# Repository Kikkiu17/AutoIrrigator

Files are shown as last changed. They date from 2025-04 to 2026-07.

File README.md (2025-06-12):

# Il progetto
Alla base del progetto c'è un microcontrollore **STM32G030F6P6**, compatto e dal costo di qualche decina di centesimi, che si interfaccia con un modulo **ESP-01S** per la connessione a Internet. Il microcontrollore può pilotare quattro elettrovalvole assieme a quattro sensori di flusso dell'acqua, uno per ogni tubo. I sensori di flusso permettono di rilevare la presenza di problemi lungo le linee e le quattro valvole consentono di irrigare fino a quattro aree alla volta.

Il tutto è **controllabile da remoto tramite un'app Android**, con la quale si possono aprire o chiudere le valvole manualmente ma si può anche impostare una programmazione per l'apertura e chiusura automatica in base all'orario o al tempo atmosferico. Infatti, il microcontrollore effettua ogni 15 minuti una richiesta all'API Open-Meteo per **ottenere le previsioni meteo della giornata**: se è prevista pioggia, è inutile irrigare, quindi le valvole resteranno chiuse.
# Costruzione
## Hardware
### Circuito stampato
Ho iniziato con l'hardware. Ho sviluppato un circuito elettronico in KiCad in modo che l'STM potesse controllare le valvole e i sensori. Le valvole sono a 12 V e consumano ~600 mA di corrente, quindi ho usato MOSFET AO3400A per poterle controllare con l'STM (i cui pin hanno un output massimo di ~15 mA a 3,3 V). Pure i sensori di flusso operano a 12 V, quindi ho usato gli stessi MOSFET per poterli interfacciare col microcontrollore.

Ho poi stampato in 3D uno stencil per poter spalmare la pasta saldante sui vari pad dei componenti a montaggio superficiale (SMD). Questo perché ordinarlo assieme alle PCB sarebbe costato quasi 20 € in più, mentre così è gratis e il risultato è comunque accettabile. Quindi perché no?

Schema:

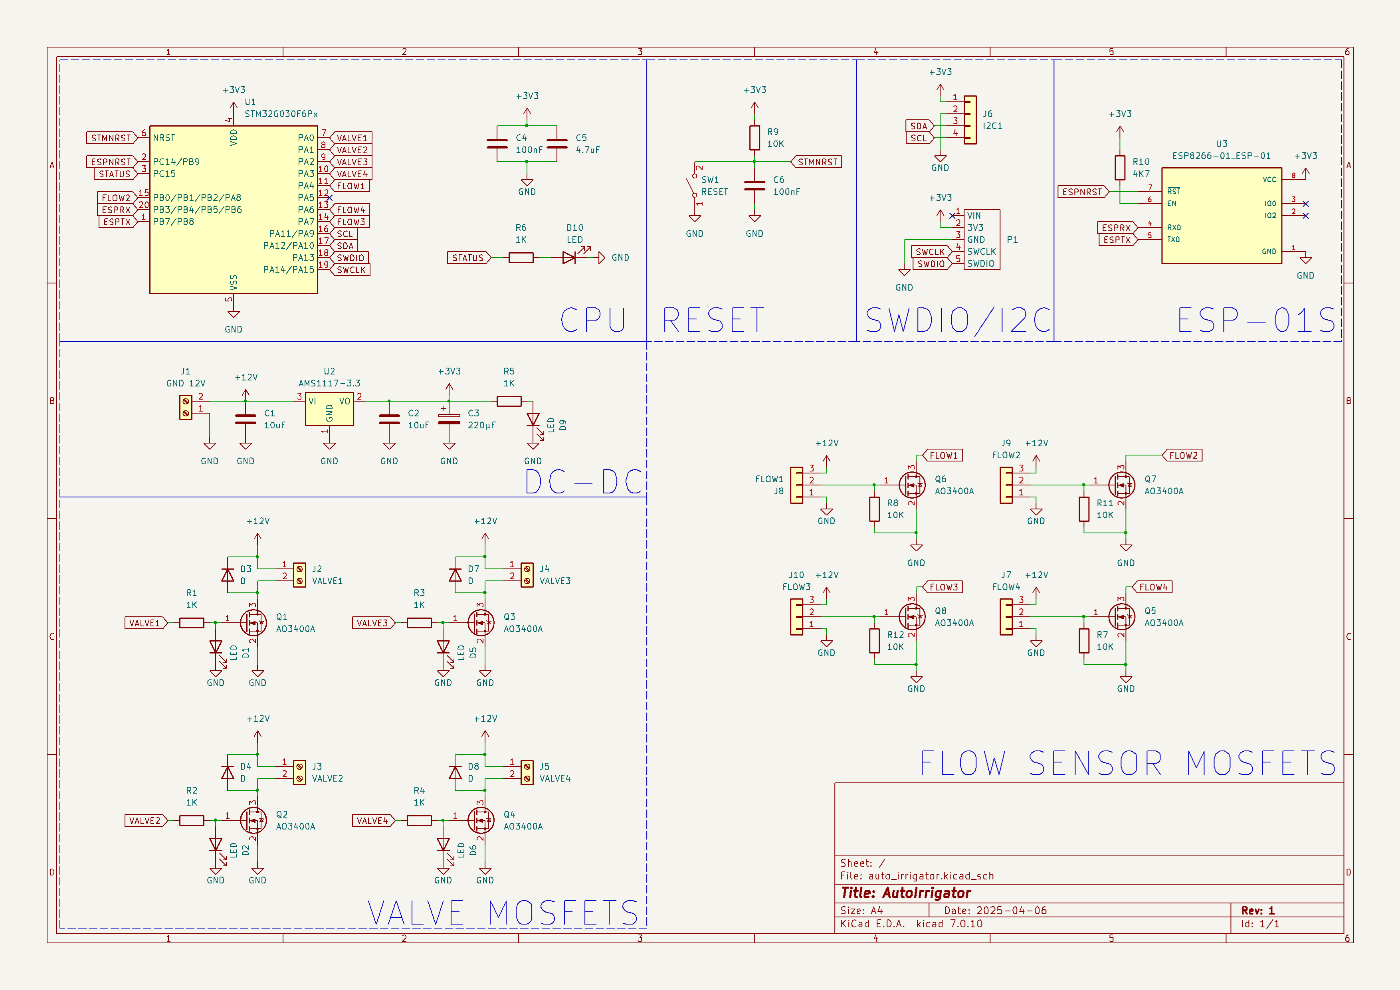
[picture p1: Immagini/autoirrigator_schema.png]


PCB:

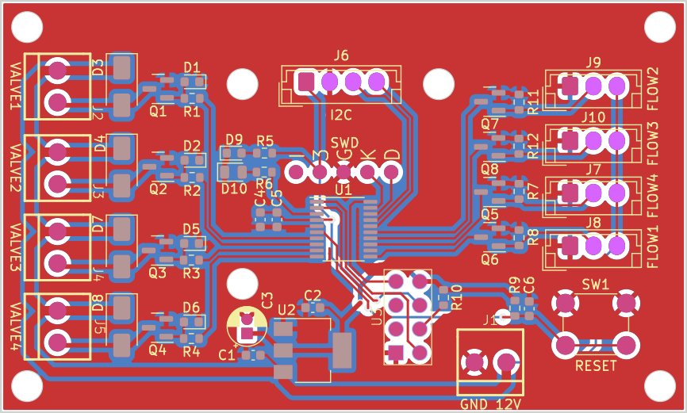
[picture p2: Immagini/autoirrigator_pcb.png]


Stencil fatto in casa


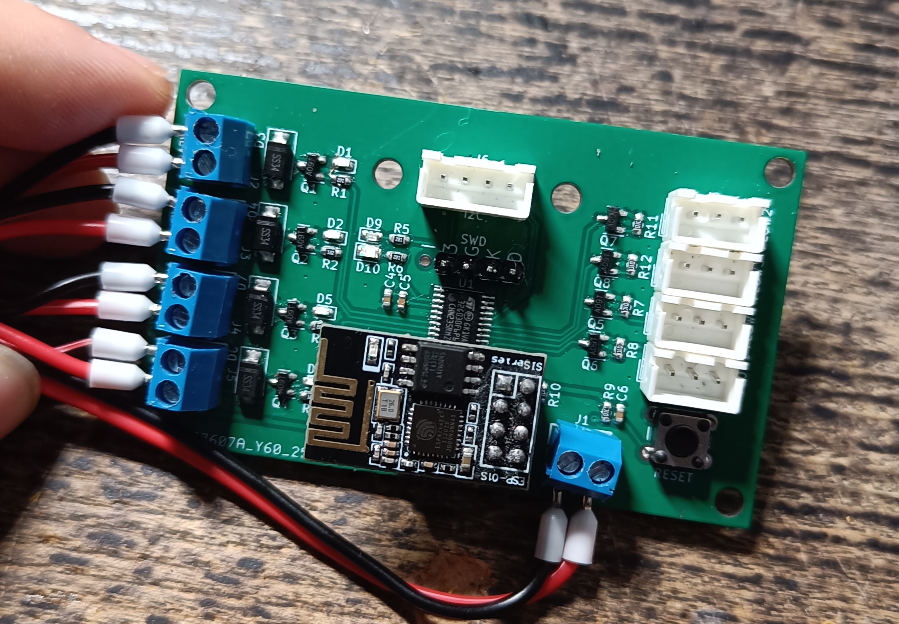
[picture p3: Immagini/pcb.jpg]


### Modello 3D
Mentre aspettavo l'arrivo delle PCB, ho iniziato a creare il modello 3D del progetto, con dei raccordi per le valvole e i sensori. Ho creato un design abbastanza compatto ma comunque semplice da assemblare, con il circuito stampato al centro in modo da poterci collegare tutti i fili comodamente.

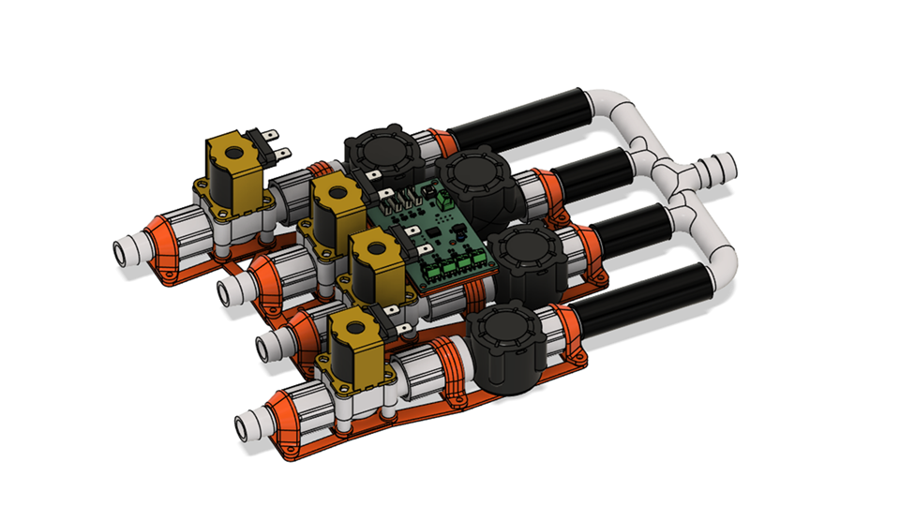
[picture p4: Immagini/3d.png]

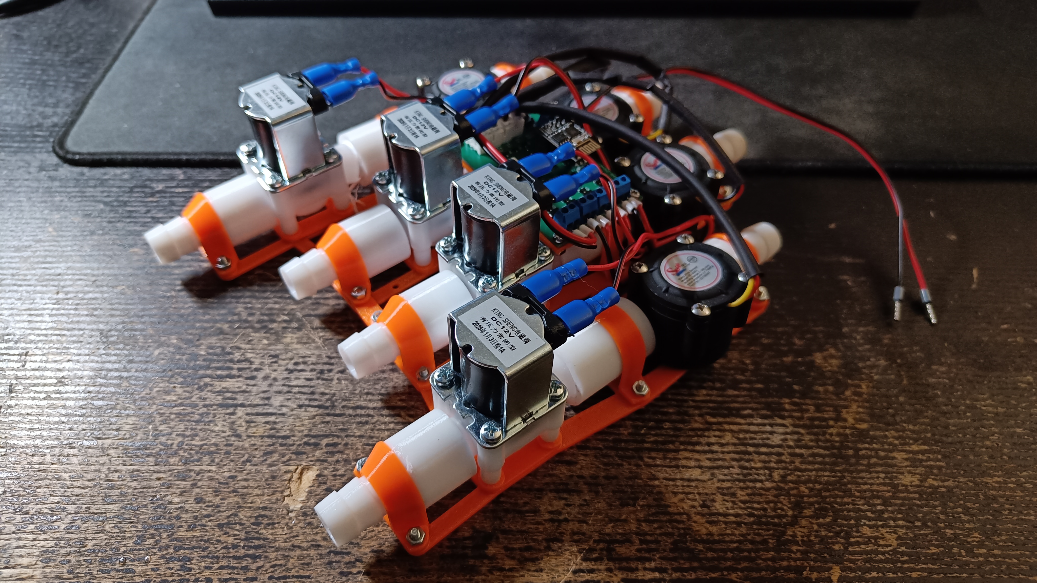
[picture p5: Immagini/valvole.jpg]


## Software
### Firmware embedded
Dopo aver fatto i raccordi e i supporti, sono passato al software. Ho iniziato a scrivere il [mio driver](https://github.com/Kikkiu17/ESP-AT-STM32) per l'ESP-01S dato che non ne ho trovato nessuno online abbastanza semplice da usare compatibile con l'STM32. Il driver sfrutta il DMA dell'STM32 per poter ricevere i dati dell'ESP dalla porta seriale senza usare la CPU, aumentando quindi le prestazioni (in questo caso le prestazioni non sono critiche, ma fa comunque comodo). L'ESP viene connesso alla rete WiFi; viene impostato l'hostname `ESPDEVICE002` per poter essere riconosciuto nella rete; viene impostato il nome `Hub irrigazione`; viene connesso al server NTP in modo da poter ottenere la data e l'ora e infine l'ESP viene impostato in modalità `server` in modo da accettare connessioni remote sulla porta `23`. Poi, nel ciclo while principale, il firmware attende nuove richieste tramite la funzione `WIFI_ReceiveRequest` che dopo verranno gestite.

Grazie ai numerosi timer dell'STM32G030F6P6, ho dedicato tre timer ai quattro sensori di flusso (chiamati FLOW): TIM14 per FLOW1, TIM1 per FLOW2, TIM3 per FLOW3 e FLOW4. In questo modo ho potuto usare quattro pin fisici per ciascun sensore, invece che fare multiplexing coi quattro sensori, rendendo quindi tutto molto più semplice. Imposto i canali timer dei sensori in modalità `Input compare` e abilito gli interrupt per i timer, in modo da ottenere il periodo del segnale PWM dei sensori. Facendo `1/T`, dove T è il periodo, si ottiene la frequenza e dividendola per 7,5 si ottiene il flusso d'acqua in `litri/min`.

Infine ho scritto del codice per connettermi all'API di Open-meteo per ottenere le [previsioni per il giorno corrente](http://api.open-meteo.com/v1/forecast?latitude=45.5582&longitude=9.2149&hourly=precipitation,precipitation_probability&current=precipitation&timezone=auto&forecast_days=1) tramite la funzione `WEATHER_GetForecast`. Le previsioni vengono immagazzinate in degli array in modo da poter accedere facilmente ad esse.

### App Android
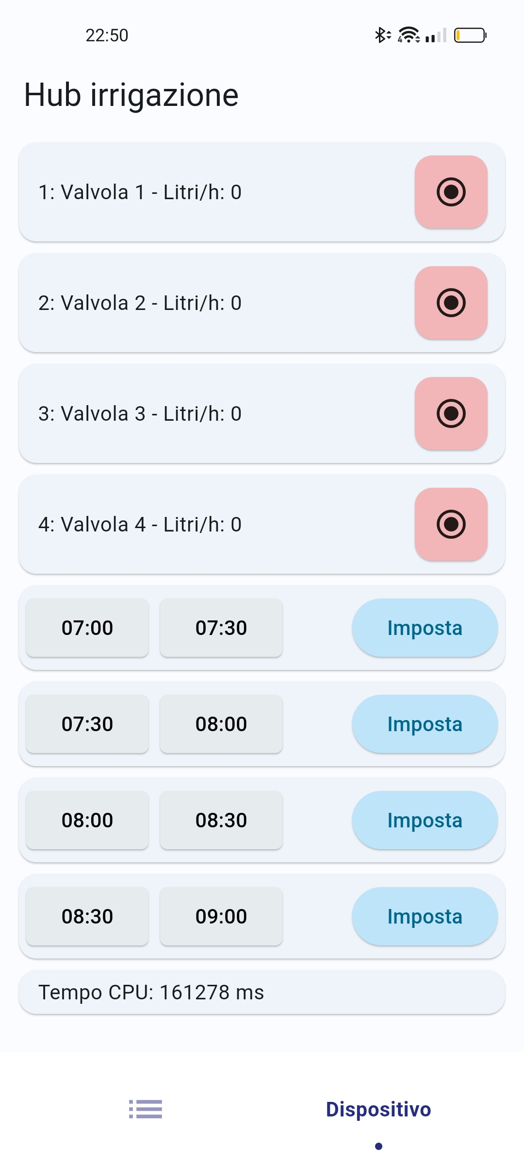
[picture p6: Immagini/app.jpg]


Per controllare il tutto si usa un'app Android, ESPValve. Volevo utilizzare l'app [ESPIOT](https://github.com/Kikkiu17/espiot) di un mio vecchio progetto, ma il modo in cui l'ho scritta rende difficile l'integrazione di nuovi dispositivi ad essa, quindi ho deciso di riscriverla da zero. La vecchia app richiedeva delle caratteristiche specifiche da chiedere ai dispositivi connessi, quindi per aggiungere, ad esempio, un pulsante, bisognava modificare in modo pesante sia l'applicazione che il dispositivo (in questo caso l'STM32 e l'ESP). La nuova app invece chiede ogni 250 ms un pacchetto di `feature` dal dispositivo con questa struttura: `tipoX$Nome,caratteristica_aggiuntiva$Nome$dato` oppure `tipoX$Nome$dato`. `tipo` è il tipo di caratteristica, quindi interruttore, bottone, sensore o timestamp e `caratteristica_aggiuntiva` può essere ad esempio `sensore`. In questo modo, posso creare il pacchetto di caratteristiche che mi interessano e l'app Android crea ogni bottone o sensore o altro col nome specificato e col dato specificato, in base alla struttura data.

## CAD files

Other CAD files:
Hardware/PCB/plots/auto_irrigator-F_Paste.dxf

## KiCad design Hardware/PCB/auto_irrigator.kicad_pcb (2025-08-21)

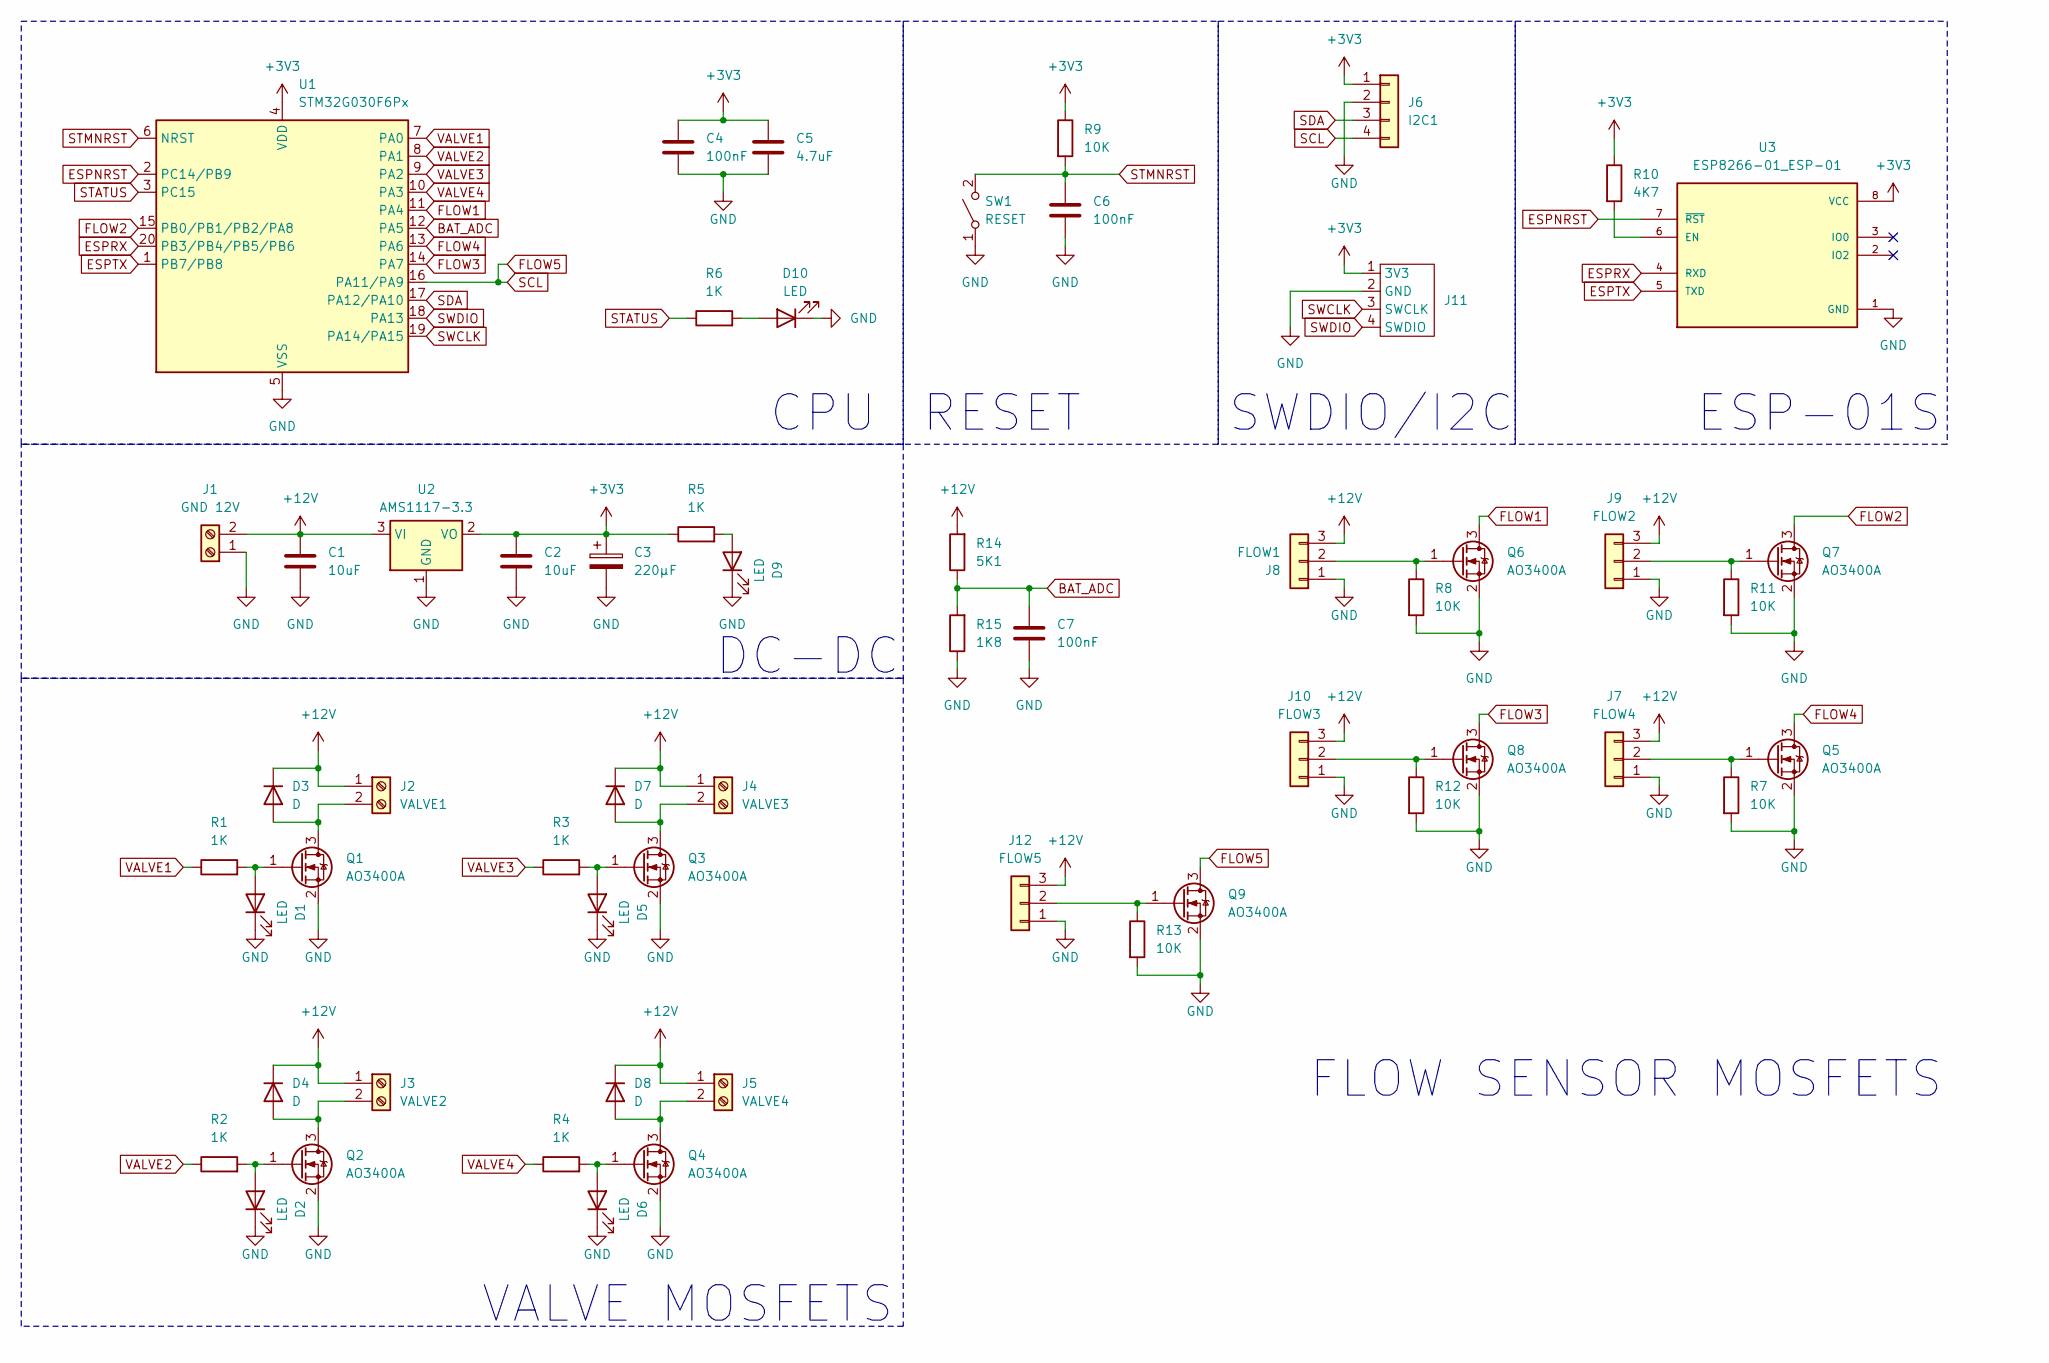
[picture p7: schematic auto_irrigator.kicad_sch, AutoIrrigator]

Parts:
C1, C2: 10uF; C_0603_1608Metric
C3: 220µF; CP_Radial_D4.0mm_P1.50mm
C4, C6, C7: 100nF; C_0603_1608Metric
C5: 4.7uF; C_0603_1608Metric
D1, D2, D5, D6, D9: LED; LED_0603_1608Metric
D3, D4, D7, D8: D; D_SMA
D10: LED; LED_0805_2012Metric
J1: GND 12V; screw_2p_small
J2: VALVE1; screw_2p_small
J3: VALVE2; screw_2p_small
J4: VALVE3; screw_2p_small
J5: VALVE4; screw_2p_small
J6: I2C1; JST_EH_B4B-EH-A_1x04_P2.50mm_Vertical
J7: FLOW4; JST_EH_B3B-EH-A_1x03_P2.50mm_Vertical
J8: FLOW1; JST_EH_B3B-EH-A_1x03_P2.50mm_Vertical
J9: FLOW2; JST_EH_B3B-EH-A_1x03_P2.50mm_Vertical
J10: FLOW3; JST_EH_B3B-EH-A_1x03_P2.50mm_Vertical
J11: swdio
J12: FLOW5; JST_EH_B3B-EH-A_1x03_P2.50mm_Vertical
Q1, Q2, Q3, Q4, Q5, Q6, Q7, Q8, Q9: AO3400A; SOT-23
R1, R2, R3, R4, R5, R6: 1K; R_0603_1608Metric
R7, R8, R9, R11, R12, R13: 10K; R_0603_1608Metric
R10: 4K7; R_0603_1608Metric
R14: 5K1; R_0603_1608Metric
R15: 1K8; R_0603_1608Metric
SW1: RESET; SW_PUSH_6mm
U1: STM32G030F6Px; TSSOP-20_4.4x6.5mm_P0.65mm
U2: AMS1117-3.3; SOT-223-3_TabPin2
U3: ESP8266-01_ESP-01; esp-01s; PARTREV V1.2

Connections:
+3V3: C2.1, C3.1, C4.1, C5.1, J6.1, J11.1 (3V3), R5.1, R9.1, R10.1, U1.4 (VDD), U2.2 (VO), U3.8 (VCC)
+12V: C1.1, D3.1 (K), D4.1 (K), D7.1 (K), D8.1 (K), J1.2, J2.1, J3.1, J4.1, J5.1, J7.3, J8.3, J9.3, J10.3, J12.3, R14.2, U2.3 (VI)
BAT_ADC: C7.1, R14.1, R15.2, U1.12 (PA5)
ESPNRST: U1.2 (PC14/PB9), U3.7 (~RST)
ESPRX: U1.20 (PB3/PB4/PB5/PB6), U3.4 (RXD)
ESPTX: U1.1 (PB7/PB8), U3.5 (TXD)
FLOW1: Q6.3 (D), U1.11 (PA4)
FLOW2: Q7.3 (D), U1.15 (PB0/PB1/PB2/PA8)
FLOW3: Q8.3 (D), U1.14 (PA7)
FLOW4: Q5.3 (D), U1.13 (PA6)
FLOW5: J6.4, Q9.3 (D), U1.16 (PA11/PA9)
GND: C1.2, C2.2, C3.2, C4.2, C5.2, C6.2, C7.2, D1.1 (K), D2.1 (K), D5.1 (K), D6.1 (K), D9.1 (K), D10.1 (K), J1.1, J6.2, J7.1, J8.1, J9.1, J10.1, J11.2 (GND), J12.1, Q1.2 (S), Q2.2 (S), Q3.2 (S), Q4.2 (S), Q5.2 (S), Q6.2 (S), Q7.2 (S), Q8.2 (S), Q9.2 (S), R7.2, R8.2, R11.2, R12.2, R13.2, R15.1, SW1.1 (A), U1.5 (VSS), U2.1 (GND), U3.1 (GND)
unnamed: D1.2 (A), Q1.1 (G), R1.2
unnamed: D2.2 (A), Q2.1 (G), R2.2
unnamed: D3.2 (A), J2.2, Q1.3 (D)
unnamed: D4.2 (A), J3.2, Q2.3 (D)
unnamed: D5.2 (A), Q3.1 (G), R3.2
unnamed: D6.2 (A), Q4.1 (G), R4.2
unnamed: D7.2 (A), J4.2, Q3.3 (D)
unnamed: D8.2 (A), J5.2, Q4.3 (D)
unnamed: D9.2 (A), R5.2
unnamed: D10.2 (A), R6.2
unnamed: J7.2, Q5.1 (G), R7.1
unnamed: J8.2, Q6.1 (G), R8.1
unnamed: J9.2, Q7.1 (G), R11.1
unnamed: J10.2, Q8.1 (G), R12.1
unnamed: J12.2, Q9.1 (G), R13.1
unnamed: R10.2, U3.6 (EN)
SDA: J6.3, U1.17 (PA12/PA10)
STATUS: R6.1, U1.3 (PC15)
STMNRST: C6.1, R9.2, SW1.2 (B), U1.6 (NRST)
SWCLK: J11.3 (SWCLK), U1.19 (PA14/PA15)
SWDIO: J11.4 (SWDIO), U1.18 (PA13)
VALVE1: R1.1, U1.7 (PA0)
VALVE2: R2.1, U1.8 (PA1)
VALVE3: R3.1, U1.9 (PA2)
VALVE4: R4.1, U1.10 (PA3)

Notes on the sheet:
RESET
CPU
SWDIO/I2C
VALVE MOSFETS
DC-DC
ESP-01S
FLOW SENSOR MOSFETS

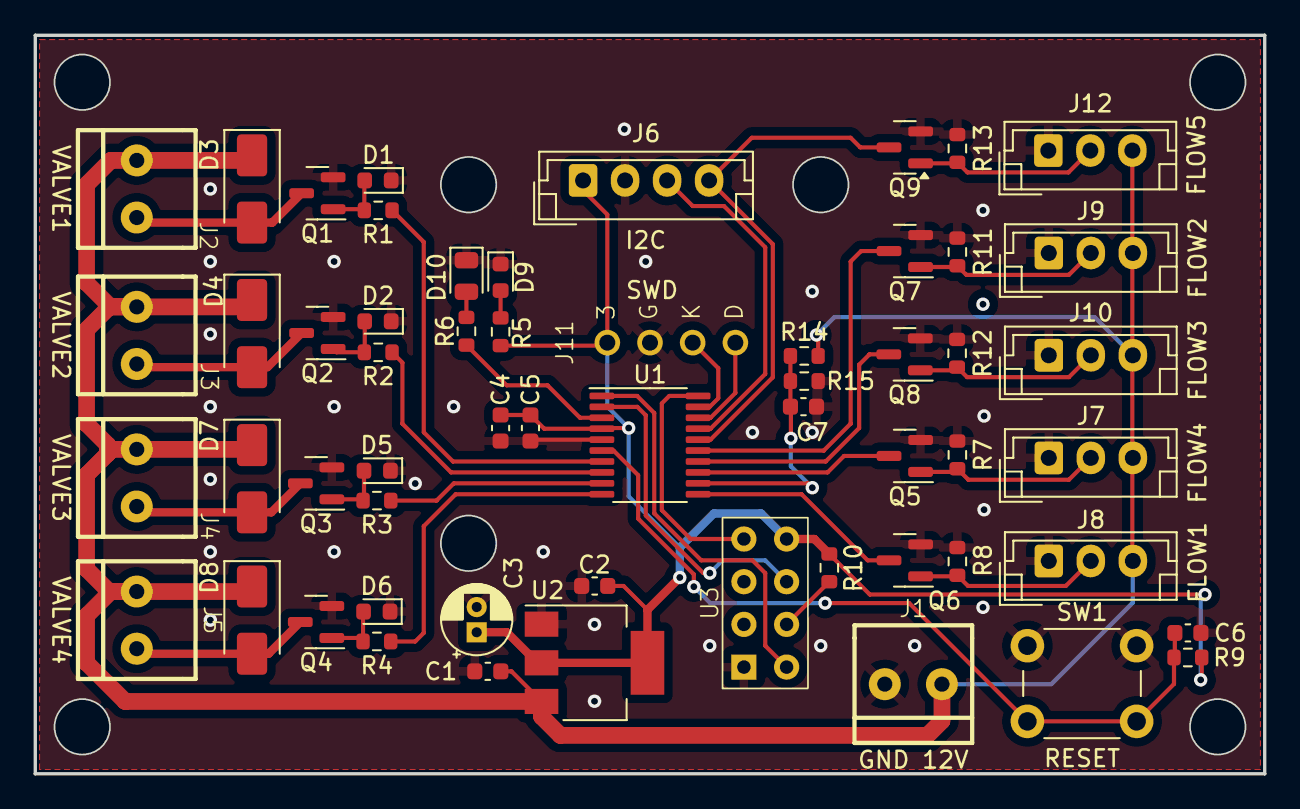
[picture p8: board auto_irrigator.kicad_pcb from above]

Board: 2 copper layers, 73.2 x 43.9 mm, 57 parts (0 on the bottom side), 37 nets.

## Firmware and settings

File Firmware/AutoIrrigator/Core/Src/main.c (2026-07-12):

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
/* Includes ------------------------------------------------------------------*/
#include "main.h"
#include "adc.h"
#include "dma.h"
#include "tim.h"
#include "usart.h"
#include "gpio.h"

/* USER CODE BEGIN Includes */
#include <string.h>
#include <stdio.h>

#include "../ESP8266/esp8266.h"
#include "../wifihandler/wifihandler.h"
#include "../credentials.h"
#include "../irrigator/irrigator.h"
#include "../settings.h"
#include "../weather/weather.h"
/* USER CODE END Includes */

/* USER CODE BEGIN PTD */
Battery_t bat;
/* USER CODE END PTD */

/* USER CODE BEGIN PM */
#define BAT_ADC_CALIBRATION_VALUE 2128 / 600
/* USER CODE END PM */


/* USER CODE BEGIN PV */
const uint32_t MAX_FLOW_PERIOD = 1 / ((float)MIN_WATER_FLOW / 60.0 * 7.5) * 1000;

uint8_t time_hour;
uint8_t time_minute;

WIFI_t wifi;

Valve_t valve_list[VALVES_NUM];
Flow_t flow1;
Flow_t flow2;
Flow_t flow3;
Flow_t flow4;
Schedule_t schedule1;
Schedule_t schedule2;
Schedule_t schedule3;
Schedule_t schedule4;

Weather_t weather;
int8_t yesterday_last_precipitation_hour;
/* USER CODE END PV */

void SystemClock_Config(void);
/* USER CODE BEGIN PFP */
void BATTERY_GetVoltage(void);
/* USER CODE END PFP */

/**
  * @brief  The application entry point.
  * @retval int
  */
int main(void)
{

  /* MCU Configuration--------------------------------------------------------*/

  /* Reset of all peripherals, Initializes the Flash interface and the Systick. */
  HAL_Init();

  /* Configure the system clock */
  SystemClock_Config();

  /* Initialize all configured peripherals */
  MX_GPIO_Init();
  MX_DMA_Init();
  MX_TIM1_Init();
  MX_TIM3_Init();
  MX_TIM14_Init();
  MX_USART1_UART_Init();
  MX_ADC1_Init();
  /* USER CODE BEGIN 2 */
  // ESPRST is HIGH by default (set up in .ioc file) so ESP is enabled by default
  if (ESP8266_Init() == TIMEOUT)
  {
	while (1)
		__NOP();
  }

#ifdef ENABLE_SAVE_TO_FLASH
  FLASH_ReadSaveData();
  if (WIFI_SetName(&wifi, savedata.name) == ERR)
    WIFI_SetName(&wifi, (char*)ESP_NAME); // happens when there is nothing saved to FLASH, so set default name
  WIFI_SetIP(&wifi, savedata.ip);         // if there is nothing saved to FLASH, this function does nothing
#else
  WIFI_SetName(&wifi, (char*)ESP_NAME);
#endif

  memcpy(wifi.SSID, ssid, strlen(ssid));
  memcpy(wifi.pw, password, strlen(password));
  HAL_GPIO_WritePin(STATUS_Port, STATUS_Pin, 1);
  uint32_t connect_status = WIFI_Connect(&wifi);
  if (connect_status == FAIL || connect_status == ERROR)
  {
    // try again
    NVIC_SystemReset();
  }
  HAL_GPIO_WritePin(STATUS_Port, STATUS_Pin, 0);
  WIFI_EnableNTPServer(&wifi, 0);

  /*
  The first time the ESP connects to WiFi, the gateway assigns an IP to it, which now gets saved to FLASH.
  The next time the ESP connects, the gateway could assign a different IP; to prevent this, the function
  WIFI_SetIP(&wifi, savedata.ip); loads the IP previously saved on FLASH so that the ESP tries to connect
  and get this IP
  */
  strncpy(savedata.ip, wifi.IP, 15);
  FLASH_WriteSaveData();

  HAL_TIM_IC_Start_IT(&htim14, TIM_CHANNEL_1);
  HAL_TIM_IC_Start_IT(&htim1, TIM_CHANNEL_1);
  HAL_TIM_IC_Start_IT(&htim3, TIM_CHANNEL_1);
  HAL_TIM_IC_Start_IT(&htim3, TIM_CHANNEL_2);

  VALVE_Init(&valve_list[0], &flow1, &schedule1, 1, VALVE1_GPIO_Port, VALVE1_Pin);
  VALVE_Init(&valve_list[1], &flow2, &schedule2, 2, VALVE2_GPIO_Port, VALVE2_Pin);
  VALVE_Init(&valve_list[2], &flow3, &schedule3, 3, VALVE3_GPIO_Port, VALVE3_Pin);
  VALVE_Init(&valve_list[3], &flow4, &schedule4, 4, VALVE4_GPIO_Port, VALVE4_Pin);

  WEATHER_GetForecast(&weather, ESP8266_GetBuffer());
  SCHEDULE_ReadFromFlash(valve_list, VALVES_NUM);

  HAL_ADCEx_Calibration_Start(&hadc1);

  if (connect_status == OK)
  {
    if (WIFIHANDLER_MQTT_Init(&wifi, MQTT_BROKER_IP, MQTT_BROKER_PORT) == OK) 
    {
      WIFIHANDLER_MQTT_PublishDiscovery(&wifi);
      WIFIHANDLER_MQTT_PublishStates(&wifi, valve_list);
    }
  }
  /* USER CODE END 2 */

  /* Infinite loop */
  /* USER CODE BEGIN WHILE */
  uint32_t timestamp = 0;
  uint8_t seconds = 60;
  uint32_t last_mqtt_publish = 0;

  bool low_bat_notification = false;
  bool valves_closed_notification = false;

  while (1)
  {
    BATTERY_GetVoltage();

    HAL_GPIO_WritePin(STATUS_Port, STATUS_Pin, 1);
    WIFIHANDLER_MQTT_Loop(&wifi, valve_list);
    
    WIFIHANDLER_ReconnectIfDisconnected(&wifi);
    
    if (HAL_GetTick() - last_mqtt_publish > MQTT_PUBLISH_INTERVAL) 
    {
      last_mqtt_publish = HAL_GetTick();
      WIFIHANDLER_MQTT_PublishStates(&wifi, valve_list);
    }
    HAL_GPIO_WritePin(STATUS_Port, STATUS_Pin, 0);

    // HANDLE WATER FLOW
    // check flow for each valve
    for (uint32_t i = 0; i < VALVES_NUM; i++)
    {
      Valve_t* valve = &(valve_list[i]);
      if (valve->flow == NULL) continue;
      if (uwTick - valve->flow->ic_timestamp > MAX_FLOW_PERIOD)
        valve->flow->lt_per_hour = 0;
    }

    // get time every minute and every 15 minutes get the forecast
    if (uwTick - timestamp > (60 - seconds) * 1000)
    {
      time_hour = WIFI_GetTimeHour(&wifi);
      time_minute = WIFI_GetTimeMinutes(&wifi);
      seconds = WIFI_GetTimeSeconds(&wifi);
      timestamp = uwTick;

      // --------- UPDATE FORECAST ---------
      if (time_minute % 15 == 0)
        WEATHER_GetForecast(&weather, ESP8266_GetBuffer());

      if (time_hour == 23)
        yesterday_last_precipitation_hour = WEATHER_GetTodayLastPrecipitation(&weather);

      // --------- CLOSE VALVES WHEN BATTERY IS LOW AND SKIP EVERYTHING ---------
      if ((bat.voltage_integer == 10 && bat.voltage_decimal <= 40) || bat.voltage_integer < 10)
      {
        if (!low_bat_notification)
        {
          low_bat_notification = true;
          WIFIHANDLER_MQTT_SendNotification(&wifi, (char*)NOTIFICATION_LOW_BATTERY);
        }

        for (uint32_t i = 0; i < VALVES_NUM; i++)
          VALVE_Close(&valve_list[i]);
        continue;	// skip valves logic. weather was already updated
      }
      else
        low_bat_notification = false;

      // --------- KEEP VALVES CLOSED IF IT RAINED LESS THAN 12 HOURS AGO ---------
      bool keep_valves_closed = false;
      if (yesterday_last_precipitation_hour != -1)
      {
        uint8_t time_diff_past = 24 - yesterday_last_precipitation_hour + time_hour;
        if (time_diff_past <= 12)
          keep_valves_closed = true;
      }

      // --------- KEEP VALVES CLOSED IF IT WILL RAIN IN THE NEXT 12 HOURS ---------
      uint8_t time_diff_future = WEATHER_GetTodayNextPrecipitation(&weather) - time_hour;
      if (time_diff_future <= 12)
        keep_valves_closed = true;

      if (weather.current_precipitation >= PRECIPITATION_THRESHOLD)
        keep_valves_closed = true;

      if (keep_valves_closed && !valves_closed_notification)
      {
        valves_closed_notification = true;
        WIFIHANDLER_MQTT_SendNotification(&wifi, NOTIFICATION_WEATHER_NO_VALVE_OPEN);
      }
      else
        valves_closed_notification = false;

      // --------- CLOSE/OPEN VALVES ---------
      for (uint32_t i = 0; i < VALVES_NUM; i++)
      {
        // code executed for each valve
        Valve_t* valve = &(valve_list[i]);

        if (keep_valves_closed)
        {
          // executed when rain is last/next 12 hours
          if (!valve->has_manual_override)
            VALVE_Close(valve);
        }
        else
        {
          // executed in normal conditions (no rain)
          // open the valve following schedule only if it doesn't rain
          if (time_hour == valve->schedule->hour_open && time_minute == valve->schedule->minute_open)
          {
            valve->has_manual_override = false;
            VALVE_Open(valve);
          }
        }

        // close valve anyway (following schedule), regardless of rain/manual override
        if (time_hour == valve->schedule->hour_close && time_minute == valve->schedule->minute_close)
        {
          valve->has_manual_override = false;
          VALVE_Close(valve);
        }
      }
    }

    /* USER CODE END WHILE */

    /* USER CODE BEGIN 3 */
  }
  /* USER CODE END 3 */
}

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
/* USER CODE BEGIN 4 */
void BATTERY_GetVoltage(void)
{
	HAL_ADC_Start(&hadc1);
	HAL_ADC_PollForConversion(&hadc1, 250);
	bat.voltage_mv = HAL_ADC_GetValue(&hadc1) * BAT_ADC_CALIBRATION_VALUE;
	bat.voltage_integer = bat.voltage_mv / 1000;
	bat.voltage_decimal = (bat.voltage_mv - bat.voltage_integer * 1000) / 10;
}

void HAL_TIM_IC_CaptureCallback(TIM_HandleTypeDef *htim)
{
	if (htim->Instance == TIM14 && htim->Channel == HAL_TIM_ACTIVE_CHANNEL_1)
	{
		// FLOW1, VALVE1
		// TIM14 only has one channel
		uint32_t val = HAL_TIM_ReadCapturedValue(htim, TIM_CHANNEL_1);
		valve_list[0].flow->ic_val = val;
		FLOW_CalculateFlow(valve_list[0].flow);
	}
	else if (htim->Instance == TIM1 && htim->Channel == HAL_TIM_ACTIVE_CHANNEL_1)
	{
		// FLOW2
		uint32_t val = HAL_TIM_ReadCapturedValue(htim, TIM_CHANNEL_1);
		valve_list[1].flow->ic_val = val;
		FLOW_CalculateFlow(valve_list[1].flow);
	}
	else if (htim->Instance == TIM3 && htim->Channel)
	{
		if (htim->Channel == HAL_TIM_ACTIVE_CHANNEL_1)
		{
			// FLOW4
			uint32_t val = HAL_TIM_ReadCapturedValue(htim, TIM_CHANNEL_1);
			valve_list[3].flow->ic_val = val;
			FLOW_CalculateFlow(valve_list[3].flow);
		}
		else if (htim->Channel == HAL_TIM_ACTIVE_CHANNEL_2)
		{
			// FLOW3
			uint32_t val = HAL_TIM_ReadCapturedValue(htim, TIM_CHANNEL_2);
			valve_list[2].flow->ic_val = val;
			FLOW_CalculateFlow(valve_list[2].flow);
		}
	}
}
/* USER CODE END 4 */
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


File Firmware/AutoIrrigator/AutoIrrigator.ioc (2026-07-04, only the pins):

Mcu.UserName=STM32G030F6Px
PA0.GPIO_Label=VALVE1
PA0.Signal=GPIO_Output
PA1.GPIO_Label=VALVE2
PA1.Signal=GPIO_Output
PA13.Signal=SYS_SWDIO
PA14-BOOT0.Signal=SYS_SWCLK
PA2.GPIO_Label=VALVE3
PA2.Signal=GPIO_Output
PA3.GPIO_Label=VALVE4
PA3.Signal=GPIO_Output
PA4.GPIO_Label=FLOW1
PA4.Signal=S_TIM14_CH1
PA5.GPIO_Label=BAT
PA5.Signal=ADC1_IN5
PA6.GPIO_Label=FLOW4
PA6.Signal=S_TIM3_CH1
PA7.GPIO_Label=FLOW3
PA7.Signal=S_TIM3_CH2
PA8.GPIO_Label=FLOW2
PA8.Signal=S_TIM1_CH1
PB6.Signal=USART1_TX
PB7.Signal=USART1_RX
PB9.GPIO_Label=ESPRST
PB9.Signal=GPIO_Output

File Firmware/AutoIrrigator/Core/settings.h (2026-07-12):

/*
 * features.h
 *
 *  Created on: Aug 6, 2025
 *      Author: kikkiu
 */

#ifndef SETTINGS_H_
#define SETTINGS_H_

#include <inttypes.h>
#include "stm32g0xx.h"

typedef uint8_t bool;
#define true 1
#define false 0

// CHANGE THESE SETTINGS ACCORDING TO YOUR SETUP!!!
#define STM_UART					huart1
#define UART_DMA_CHANNEL_HANDLE		DMA1_Channel1
#define UART_DMA_LL_CHANNEL			LL_DMA_CHANNEL_1
#define UART_DMA_TYPEDEF			DMA1
#define ESP_RST_PORT				ESPRST_GPIO_Port
#define ESP_RST_PIN					ESPRST_Pin

#define STATUS_Port					STATUS_GPIO_Port
//#define STATUS_Pin					STATUS_Pin

// if START_ATTEMPTS is set to -1, the program won't start until it receives
// "ready" from the ESP (infinite retries)
#define START_ATTEMPTS -1

// ==========================================================================================
// 										USER DEFINES
// ==========================================================================================

// ==========================================================================================
// 											FLASH
// ==========================================================================================
/**
 *				!!!THE LAST PAGE OF THE FLASH MEMORY HAS TO BE BLANK!!!
 * 						!!!CHECK PROGRAM SIZE BEFORE UPLOADING!!!
 */
#define ENABLE_SAVE_TO_FLASH

#ifdef ENABLE_SAVE_TO_FLASH
// check your datasheet for the permitted datatype! STM32G030 can write DWORD on FLASH
typedef uint64_t FLASH_DATATYPE;
#define FLASH_DATASIZE sizeof(FLASH_DATATYPE)
#define LAST_PAGE_ADDRESS 0x08000000 + ((FLASH_PAGE_NB - 1) * FLASH_PAGE_SIZE)
//#define LAST_PAGE_ADDRESS 0x08000000 + FLASH_BANK_SIZE - FLASH_PAGE_SIZE
//#define LAST_PAGE_ADDRESS 0x8007800	// check your datasheet!!!
#endif

// ==========================================================================================
// 									NETWORK (esp8266.h)
// ==========================================================================================
static const char RADIO_POWER[] = "65";

static const char ESP_NAME[] = "SNSE device";

static const char ESP_HOSTNAME[] = "SNSEDEVICE89AF"; // template: SNSEDEVICExx
static const char MQTT_BROKER_IP[] = "192.168.1.2";
static const uint16_t MQTT_BROKER_PORT = 1883;
static const uint16_t MQTT_PUBLISH_INTERVAL = 1000;	// ms

#define AT_SHORT_TIMEOUT 250
#define AT_MEDIUM_TIMEOUT 500
#define AT_LONG_TIMEOUT 1250

// BUFFERS SIZES (in RAM)

/**
 * RESPONSE_MAX_SIZE
 *
 * this buffer will contain the data to be sent FROM THIS device to the connected device
 * this could correspond to sizeof(FEATURES_TEMPLATE), because it's usually the biggest response
 * this device will send. set this according to your needs
 */
#define RESPONSE_MAX_SIZE 1024

/**
 * REQUEST_MAX_SIZE
 *
 * if you don't expect big requests from the remote device, this buffer can be small (usually 128 bytes or less)
 */
#define REQUEST_MAX_SIZE 256

/**
 * WIFI_BUF_MAX_SIZE
 *
 * the longest content is usually the FEATURES array, so the minimum size should be the size of
 * FEATURES_TEMPLATE. usually this is the reason of most hard faults, so try increasing it
 */
#define WIFI_BUF_MAX_SIZE 800

/**
 * UART_BUFFER_SIZE
 *
 * if you have to retrieve large amounts of data (i.e. from an API), set this to the minimum size of the response
 * otherwise, it can be smaller.
 * if you don't have these requirements, you can set it to a minimum of
 * REQUEST_MAX_SIZE + some headroom to avoid receiving only partial messages
 * if you encounter weird behaviors at runtime, try increasing this buffer size
 */
#define UART_BUFFER_SIZE 1536

#define HOSTNAME_MAX_SIZE 32		// ESPDEVICExxx
#define NAME_MAX_SIZE 32			// human-readable name

#define UART_TX_TIMEOUT 500			// ms
#define UART_RX_IDLE_TIMEOUT 3000	// ms

#define RECONNECTION_DELAY_MINS 1	// minutes
#define RECONNECTION_DELAY_MILLIS RECONNECTION_DELAY_MINS * 60000

typedef struct
{
	char* text;
	uint8_t size;
	bool read;
	bool clear_if_read;
} Notification_t;

extern Notification_t notification;	// defined in wifihandler/wifihandler.c

// ==========================================================================================
// 									IRRIGATION / SCHEDULE
// ==========================================================================================
#define VALVES_NUM 4
#define MIN_WATER_FLOW 30			// liters per hour
#define SCHEDULE_TIME_SIZE 11		// hh:mm-hh:mm
#define DEFAULT_SCHEDULE "00:00-00:00"

// ==========================================================================================
// 									IRRIGATION STRUCTS
// ==========================================================================================
typedef struct flow
{
	uint32_t 			last_ic_val;
	uint32_t 			ic_val;
	uint32_t 			ic_timestamp;
	uint32_t 			period_us;
	uint32_t 			lt_per_hour;
} Flow_t;

typedef struct schedule
{
	int8_t 				hour_open;
	int8_t 				minute_open;
	int8_t 				hour_close;
	int8_t 				minute_close;
	char				text[SCHEDULE_TIME_SIZE+1];
} Schedule_t;
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

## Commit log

2025-04-26 Aggiunta funzioni
    Aggiunte funzioni WEATHER per ottenere le previsioni meteo per la giornata attuale e funzione FLOW per il calcolo del flusso d'acqua
2025-04-26 Aggiunta PCB, 3D, App Android
    [auto_irrigator-B_Cu.gbr, auto_irrigator-B_Mask.gbr, auto_irrigator-B_Paste.gbr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]
2025-05-15 Timer programmabile
2025-08-08 Bugfix render pagina & disconnessione
    Sistemato bug per cui la pagina del dispositivo rimaneva vuota cambiando menù. Sistemato bug per cui quando l'app andava in sospensione in background non si riconnetteva più al dispositivo.
2025-08-09 Salva su FLASH anche il nome
2025-08-21 AutoIrrigator rev 2
    Aggiunte notifiche. Migliorata ulteriormente la stabilità. Modificata PCB per sistemare gli errori della rev 1.
    [auto_irrigator-F_Paste.dxf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]
2025-08-25 Rimosso il BOM
2025-09-09 Aggiornato driver ESP (stabilità)
2025-09-09 Driver ESP (semplificato)
2025-09-28 Aggiornato driver ESP-AT
2025-10-03 Fixed write past the end of array
    [esp8266.c]
2025-10-03 Fixed name reading issue
    [esp8266.c]
2026-05-02 Updated ESP driver

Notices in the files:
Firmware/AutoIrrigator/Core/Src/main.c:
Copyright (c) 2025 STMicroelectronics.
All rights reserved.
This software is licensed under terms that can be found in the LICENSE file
